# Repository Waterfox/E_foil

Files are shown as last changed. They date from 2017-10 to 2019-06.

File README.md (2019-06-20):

# Electric Hydrofoil Project

This is an electric hydrofoil thruster design.

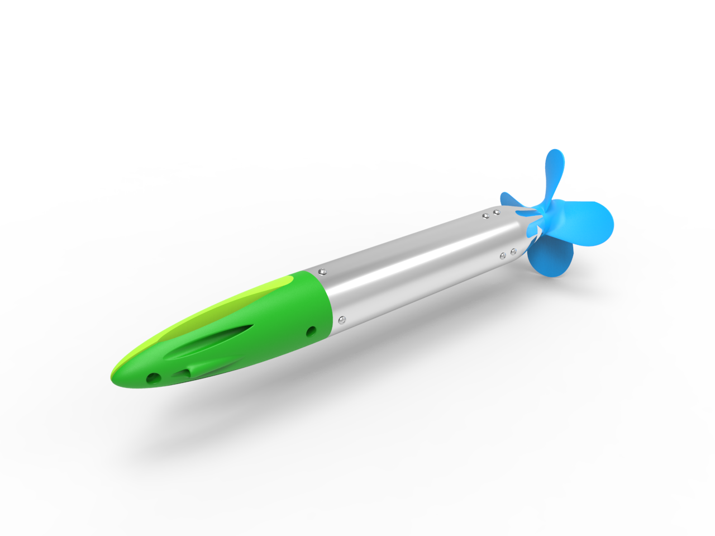
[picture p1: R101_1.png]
Thurster Render


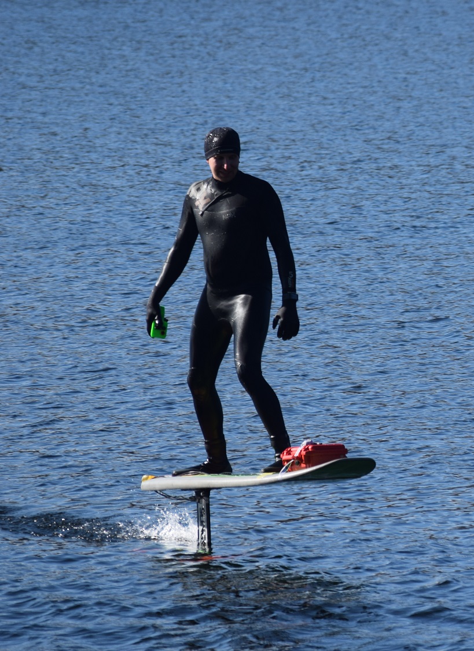
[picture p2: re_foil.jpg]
Riding Shot


Check out some of the initial test runs here on a Slingshot NF2 foil. 

[Waterproof Remote Control](https://github.com/Waterfox/Efoil-Waterproof-Controller)

<a href="http://www.youtube.com/watch?feature=player_embedded&v=rsEWBcoidBg
" target="_blank">IMAGE ALT TEXT HERE</a>

<a href="http://www.youtube.com/watch?feature=player_embedded&v=VSeLOgUywpE
" target="_blank">IMAGE ALT TEXT HERE</a>

<a href="http://www.youtube.com/watch?feature=player_embedded&v=JIKbu8u5FK8
" target="_blank">IMAGE ALT TEXT HERE</a>

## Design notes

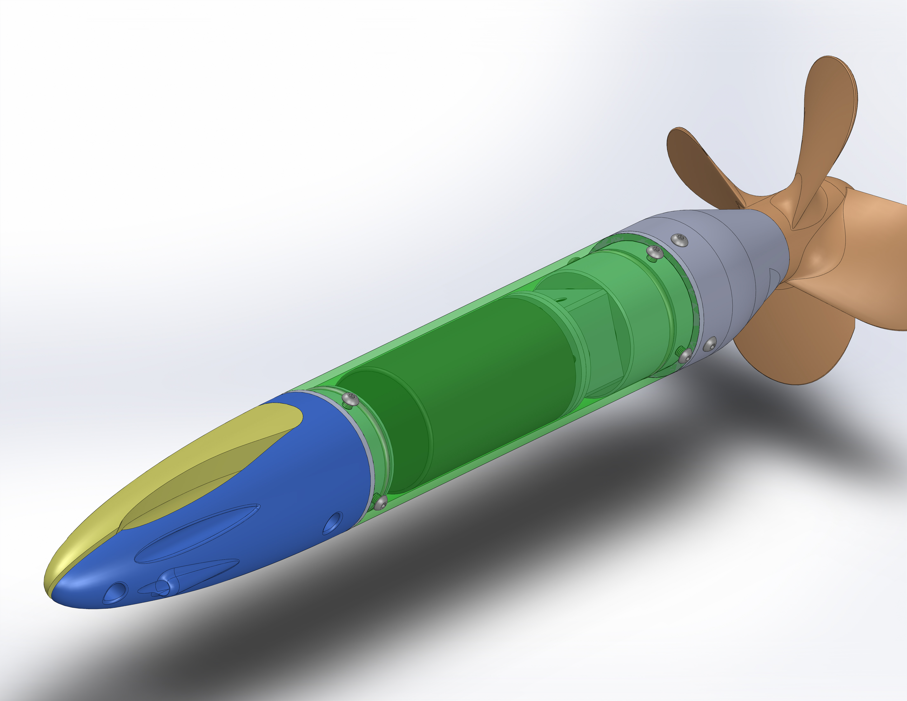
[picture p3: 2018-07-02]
R001_1 - Kitefoil Thruster Assy1.JPG

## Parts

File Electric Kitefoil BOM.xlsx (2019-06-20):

Part | Name | Description | Supplier | Part number | Cost | Currency | QTY | Mass kg | Website
R001 | Kitefoil Thruster Assy
R002 | SSS56104 500kV | Brushless Motor | Ebay |  | 160 | USD | 1 | 1.02 | http://www.ebay.com/itm/SSS-56104-500KV-6-pole-brushless-motor-/152600709580
R003 | gearbox | Neugart PLE40-008 | Ebay |  | 150 | USD | 1 | 0.35 | http://www.ebay.com/itm/NEUGART-PLE-40-GEARHEAD-REDUCER-FREE-SHIP-/251343315130
R004 | BHCS M4X0.7X6MM 18-8 |  | Mcmaster | 92095A188 |  |  | 16 |  | 92095A188
R005 | FHCS M4 X 0.7 X 8MM 18-8 |  | Mcmaster | 92125A188 | 6.5 |  | 10 |  | 92125A188
R006 | O-Ring 1/8 | 2.25 OD 2.0ID, 1/8in Dash 226 Buna-N | Mcmaster | 9452K64 | 13 | USD | 3 |  | https://www.mcmaster.com/#9452k64/=18ufglf
R007 | ESC | Hobbywing Seaking HV V3 130A | Ebay |  | 150 | USD | 1
R008 | Controller | 2.4Ghz Eskate Remote - with waterproof modification? | Ali-Express |  | 36 | USD | 1 |  | https://www.aliexpress.com/item/2-4Ghz-Remote-Controller-With-Receiver-Universal-for-All-ESC-Electric-Skateboard-Longboard-Skate-Board-Scooter/32817830821.html
R009 | Battery | Tattu Plus 6S 16000mAh |  |  |  |  | 2
R010 | Pelican Case 1200 | Pelican Case 1200 | MEC |  | 60 | CAD | 1
R011 | 8mm Shaft L= 65mm | 8mm ground shaft, 65MMLength | ? |  |  |  | 1
R012 | 8MM to 10MM Shaft Coupler | uxcell® 8mm to 10mm Elastic Shaft Coupling 30mm Length 25mm Diameter Motor Coupler Aluminum Alloy Joint Connector for DIY Encoder | Amazon | a16121900ux0451 | 10 | CAD | 1 |  | https://www.amazon.ca/dp/B06X9XSNQ2/ref=pe_3034960_233709270_TE_item
R013 | Oil Seal Bushing |  |  |  |  |  | 2
R014 | Bearing 8MM ID 11MM OD | 6153K51 | Mcmaster | 6153K51 | 12 | USD | 1 |  | 6153K51
R015 | Thrust Bearing |  | Mcmaster | 5909K11 | 3.7 | USD | 1
R015 | Thrust Bearing Washer |  | Mcmaster | 5909K71 |  |  | 2
 | Propeller shaft attachment | TBD |  |  |  |  | 1
 | 8, 10, or 12 AWG wire
 | Epoxy or Acrylic glue
 | M4 X 10MM ? | mount gearbox |  |  |  |  | 4
 | M3 X 10MM | oil seal cap |  |  |  |  | 1
 | M4 X 25MM | nose cone to front cap |  |  |  |  | 4
 | M5 X 25 | nose cone foil mount |  |  |  |  | 2
 | M5 NUT | nose cone foil mount |  |  |  |  | 2
MTS Parts
R101 | motor tube | 2.5IN OD 0.125IN WALL, 12IN Length 6061 T6 Tube | Online Metals, Mcmaster, Metal Supermarkets |  | 20 | CAD | 1 | 0.325
R102 | motor_gear_adapter_A | 6061-T6 0.125IN
R103 | motor_gear_adapter_B | 6061-T6 0.125IN
R104 | front_cap | 6061-T6 2.5IN ROUND BAR
R105 | gear_mount | 6061-T6 2.5IN ROUND BAR
R106 | shaft_cap | 6061-T6 2.5IN ROUND BAR
R107 | nose_cone_A | 3D PRINT PLA
P108 | nose_cone_B | 3D PRINT PLA
R109 | propeller | 3D PRINT PLA
R110 | reverse bushing | 3D PRINT PLA
R111 | Mast wire fairing | 3D PRINT PLA

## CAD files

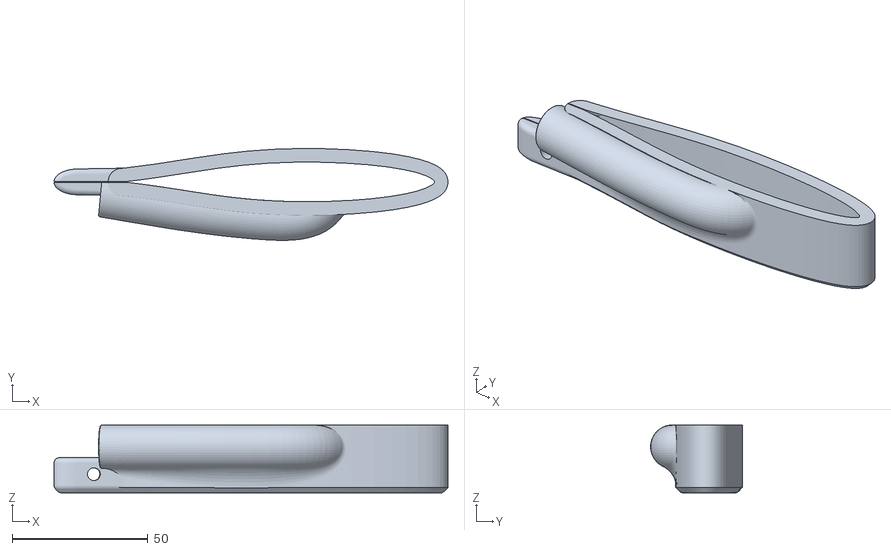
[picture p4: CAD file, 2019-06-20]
R111_1 - mast, wire fairing.STL
144.9 x 33.8 x 25.0

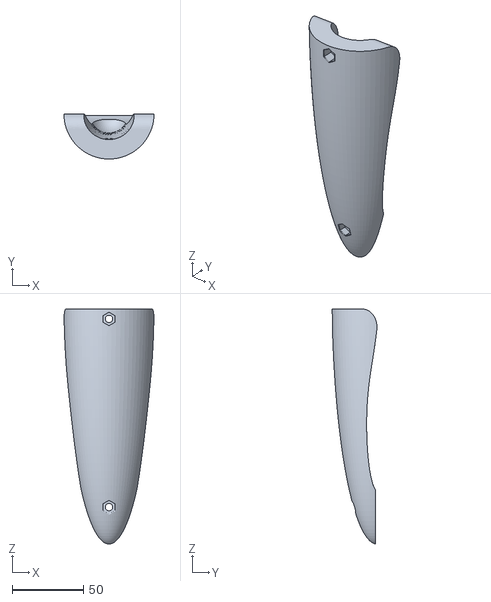
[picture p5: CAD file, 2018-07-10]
R108-GEO_2 - nose_cone_B.STL
63.0 x 31.6 x 164.9

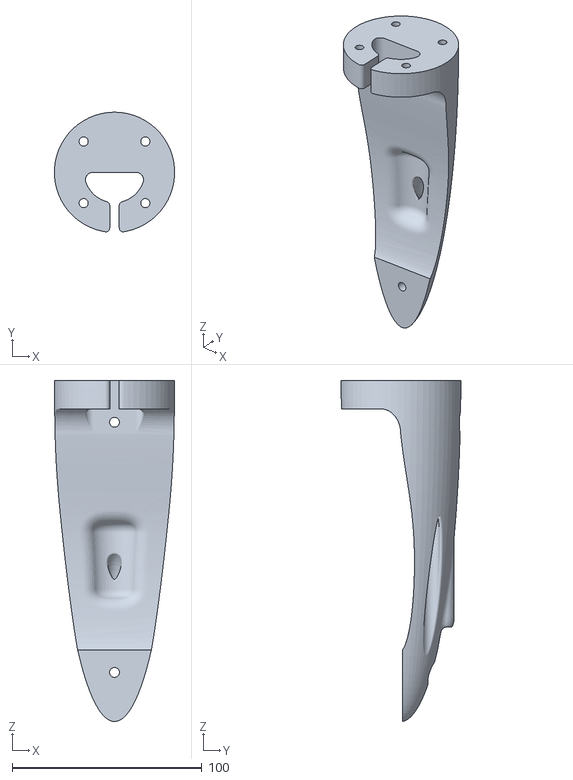
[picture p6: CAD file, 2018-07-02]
R107-GEO_2 - nose_cone_A.STL
63.4 x 63.2 x 179.9

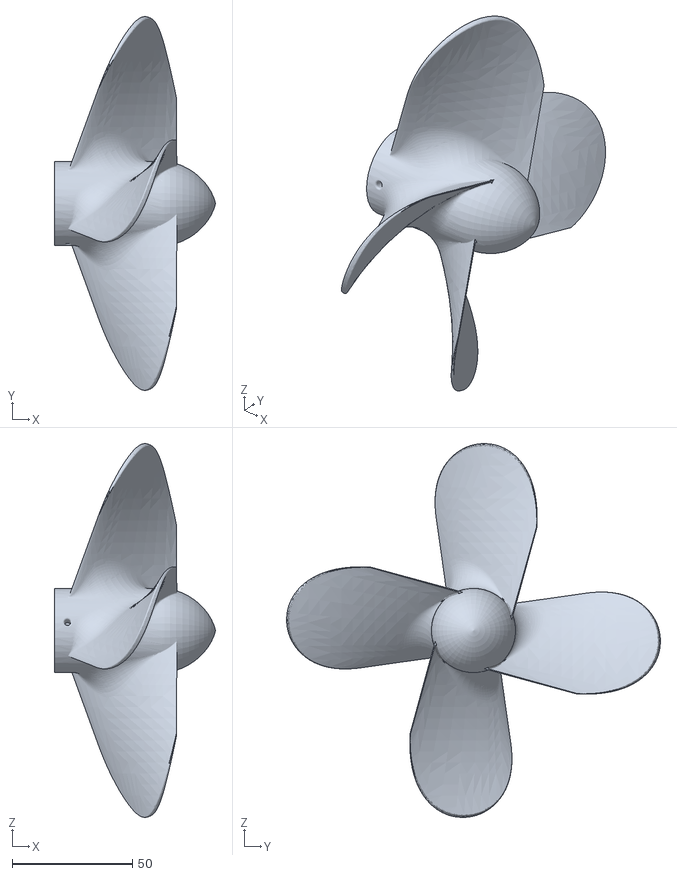
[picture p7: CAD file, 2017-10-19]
Propeller6_2_14kn4B.STL
67.0 x 155.4 x 155.4

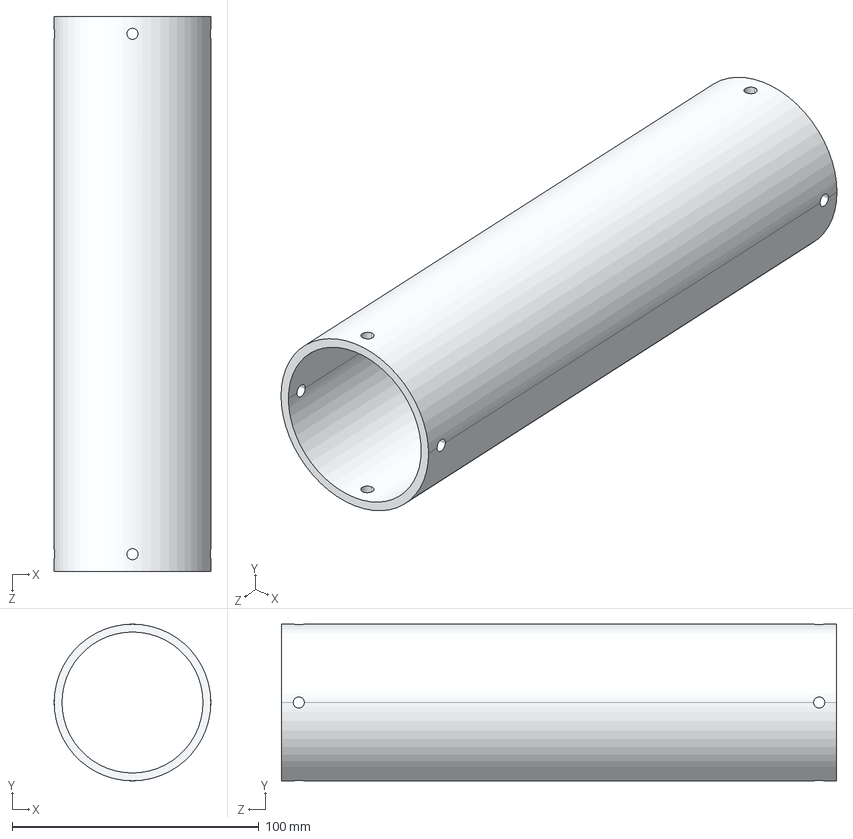
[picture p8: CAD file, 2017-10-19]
R101-GEO_1 - motor_tube.STEP
63.5 x 63.5 x 225.0 mm

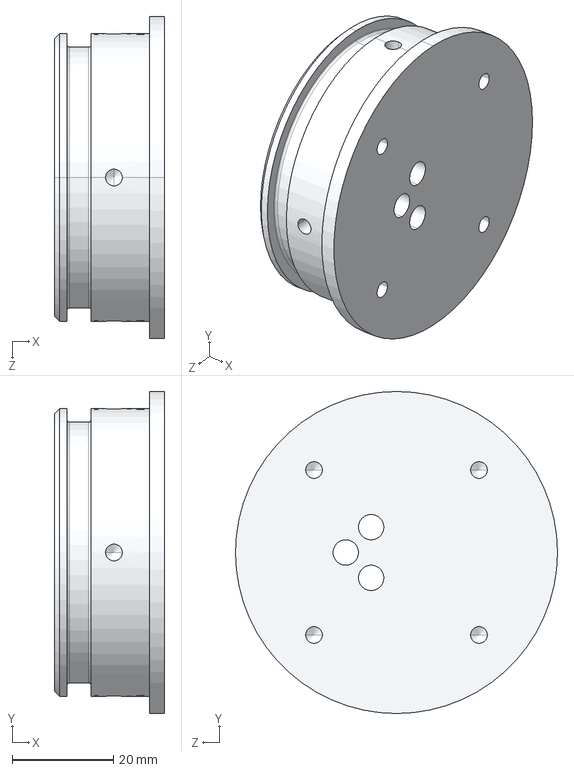
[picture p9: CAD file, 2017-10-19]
R104-GEO_1 - front_cap.STEP
21.7 x 63.5 x 63.5 mm

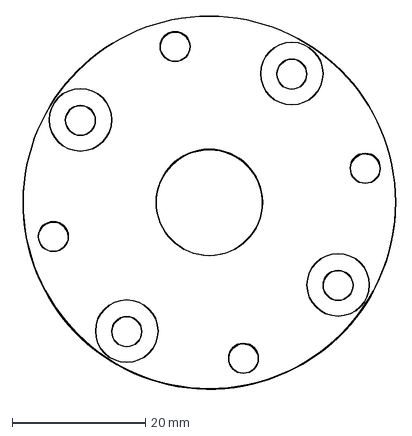
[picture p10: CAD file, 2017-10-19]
R102-GEO_1 - motor_gear_adapter_A.DXF
57.0 x 57.1 mm

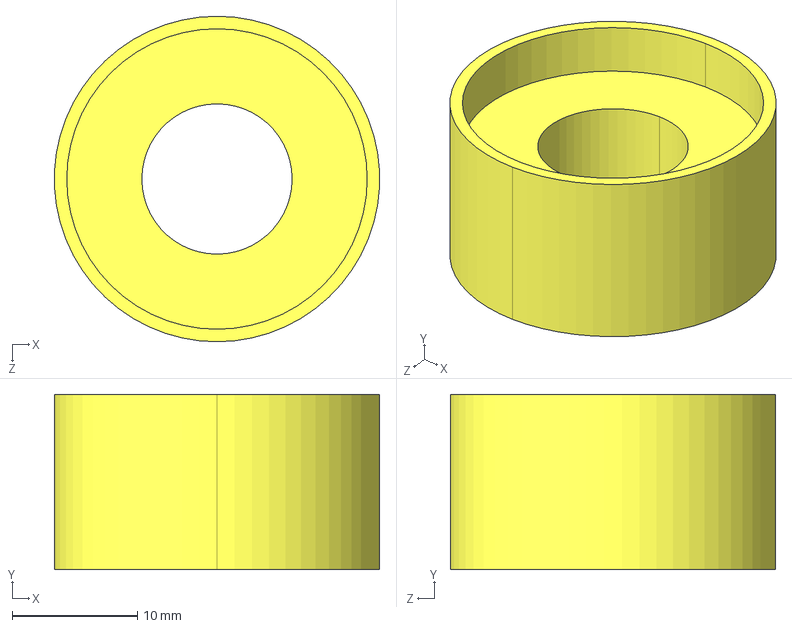
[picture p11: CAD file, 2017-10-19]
R109-GEO_1 - thrust_beaing-mount.STEP
26.0 x 14.0 x 26.0 mm

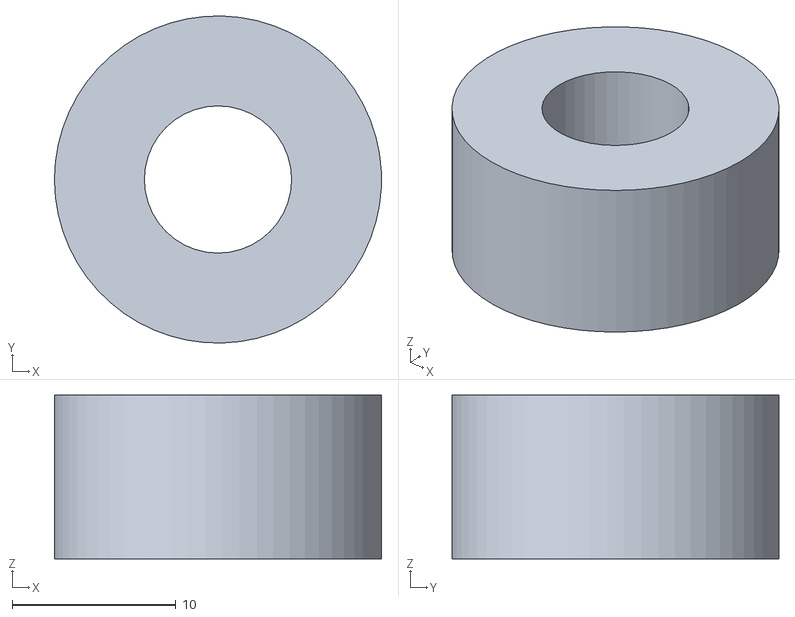
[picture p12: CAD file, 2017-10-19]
R110-GEO_2 - revBushing.STL
20.0 x 20.0 x 10.0

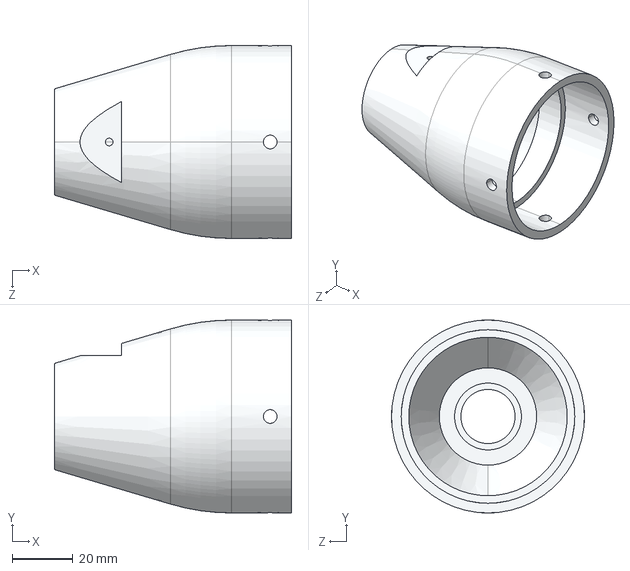
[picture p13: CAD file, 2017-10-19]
R106-GEO_1 - shaft_cap.STEP
78.0 x 63.5 x 63.5 mm

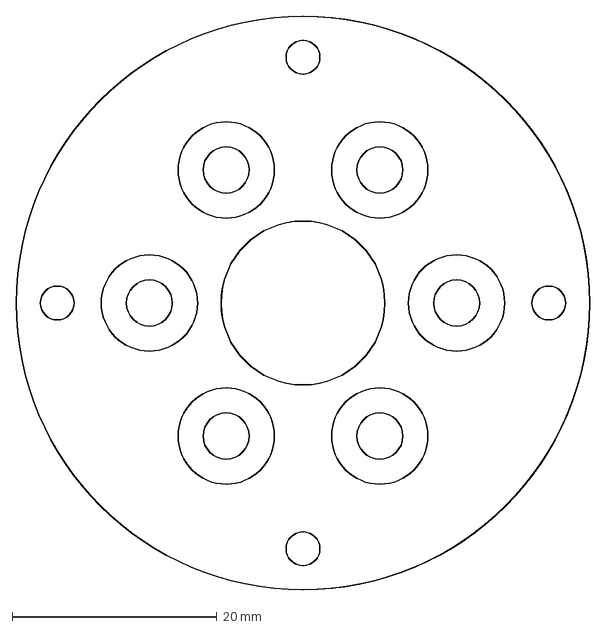
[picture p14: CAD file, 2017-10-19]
R103-GEO_1 - motor_gear_adapter_B.DXF
56.0 x 56.0 mm

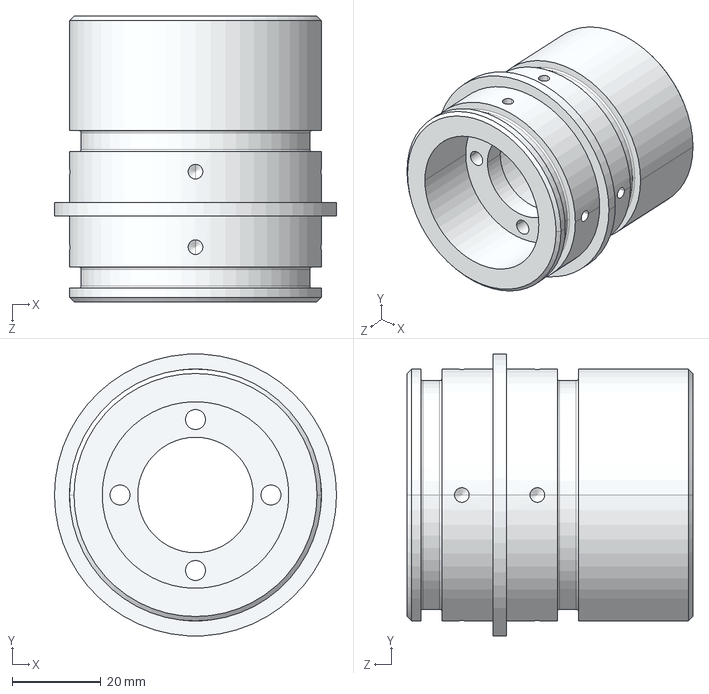
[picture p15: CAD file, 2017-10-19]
R105-GEO_1 - gear_mount.STEP
63.5 x 63.4 x 64.3 mm

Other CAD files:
Mast - wire fairing.STL

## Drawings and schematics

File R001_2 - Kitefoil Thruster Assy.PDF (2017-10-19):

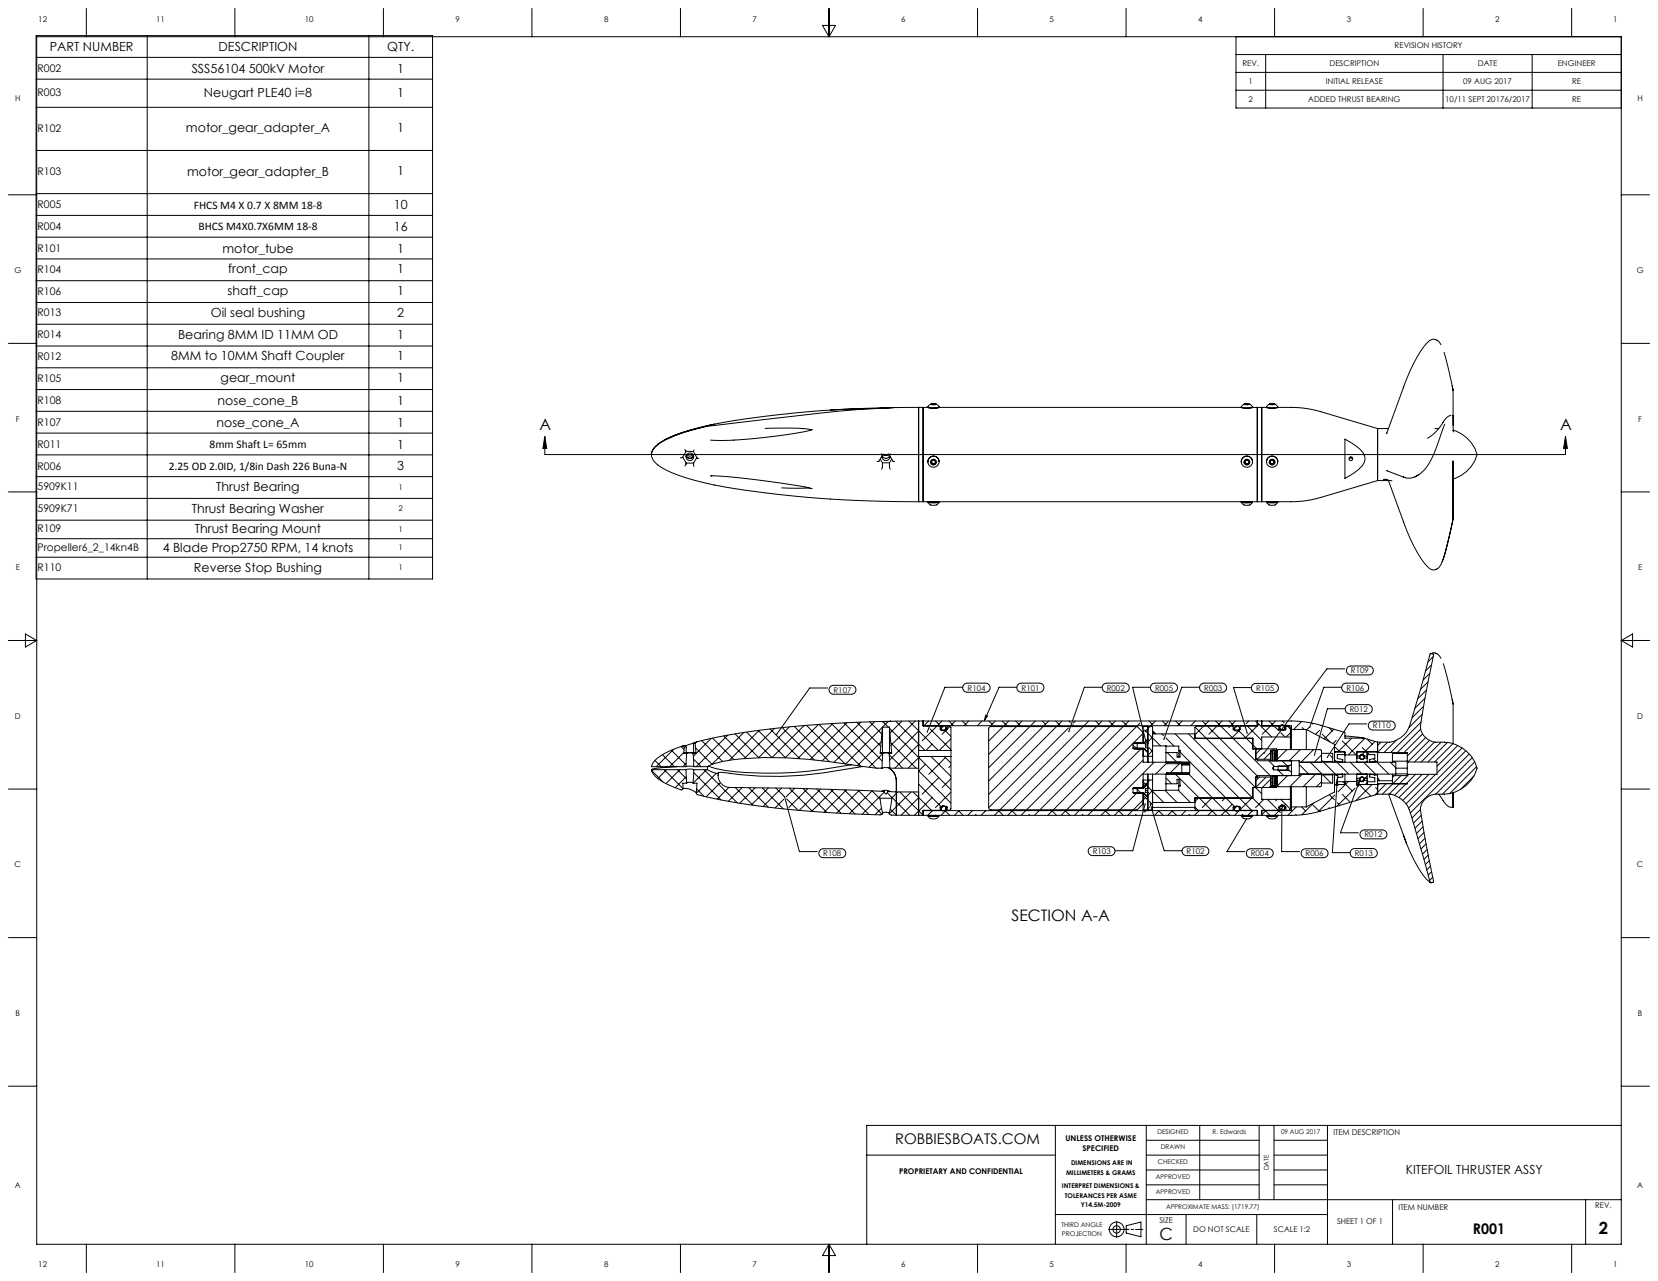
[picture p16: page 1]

R002 | SSS56104 500kV Motor | 1
R003 | Neugart PLE40 i=8 | 1

REV. | DESCRIPTION | DATE | ENGINEER
1 | INITIAL RELEASE | 09 AUG 2017 | RE
2 | ADDED THRUST BEARING | 10/11 SEPT 20176/2017 | RE

R102 | motor_gear_adapter_A | 1

R103 | motor_gear_adapter_B | 1

R005 | FHCS M4 X 0.7 X 8MM 18-8 | 10
R004 | BHCS M4X0.7X6MM 18-8 | 16
R101 | motor_tube | 1
R104 | front_cap | 1
R106 | shaft_cap | 1
R013 | Oil seal bushing | 2
R014 | Bearing 8MM ID 11MM OD | 1
R012 | 8MM to 10MM Shaft Coupler | 1
R105 | gear_mount | 1
R108 | nose_cone_B | 1
R107 | nose_cone_A | 1
R011 | 8mm Shaft L= 65mm | 1
R006 | 2.25 OD 2.0ID, 1/8in Dash 226 Buna-N | 3
5909K11 | Thrust Bearing | 1
5909K71 | Thrust Bearing Washer | 2
R109 | Thrust Bearing Mount | 1
Propeller6_2_14kn4B | 4 Blade Prop2750 RPM, 14 knots | 1
R110 | Reverse Stop Bushing | 1

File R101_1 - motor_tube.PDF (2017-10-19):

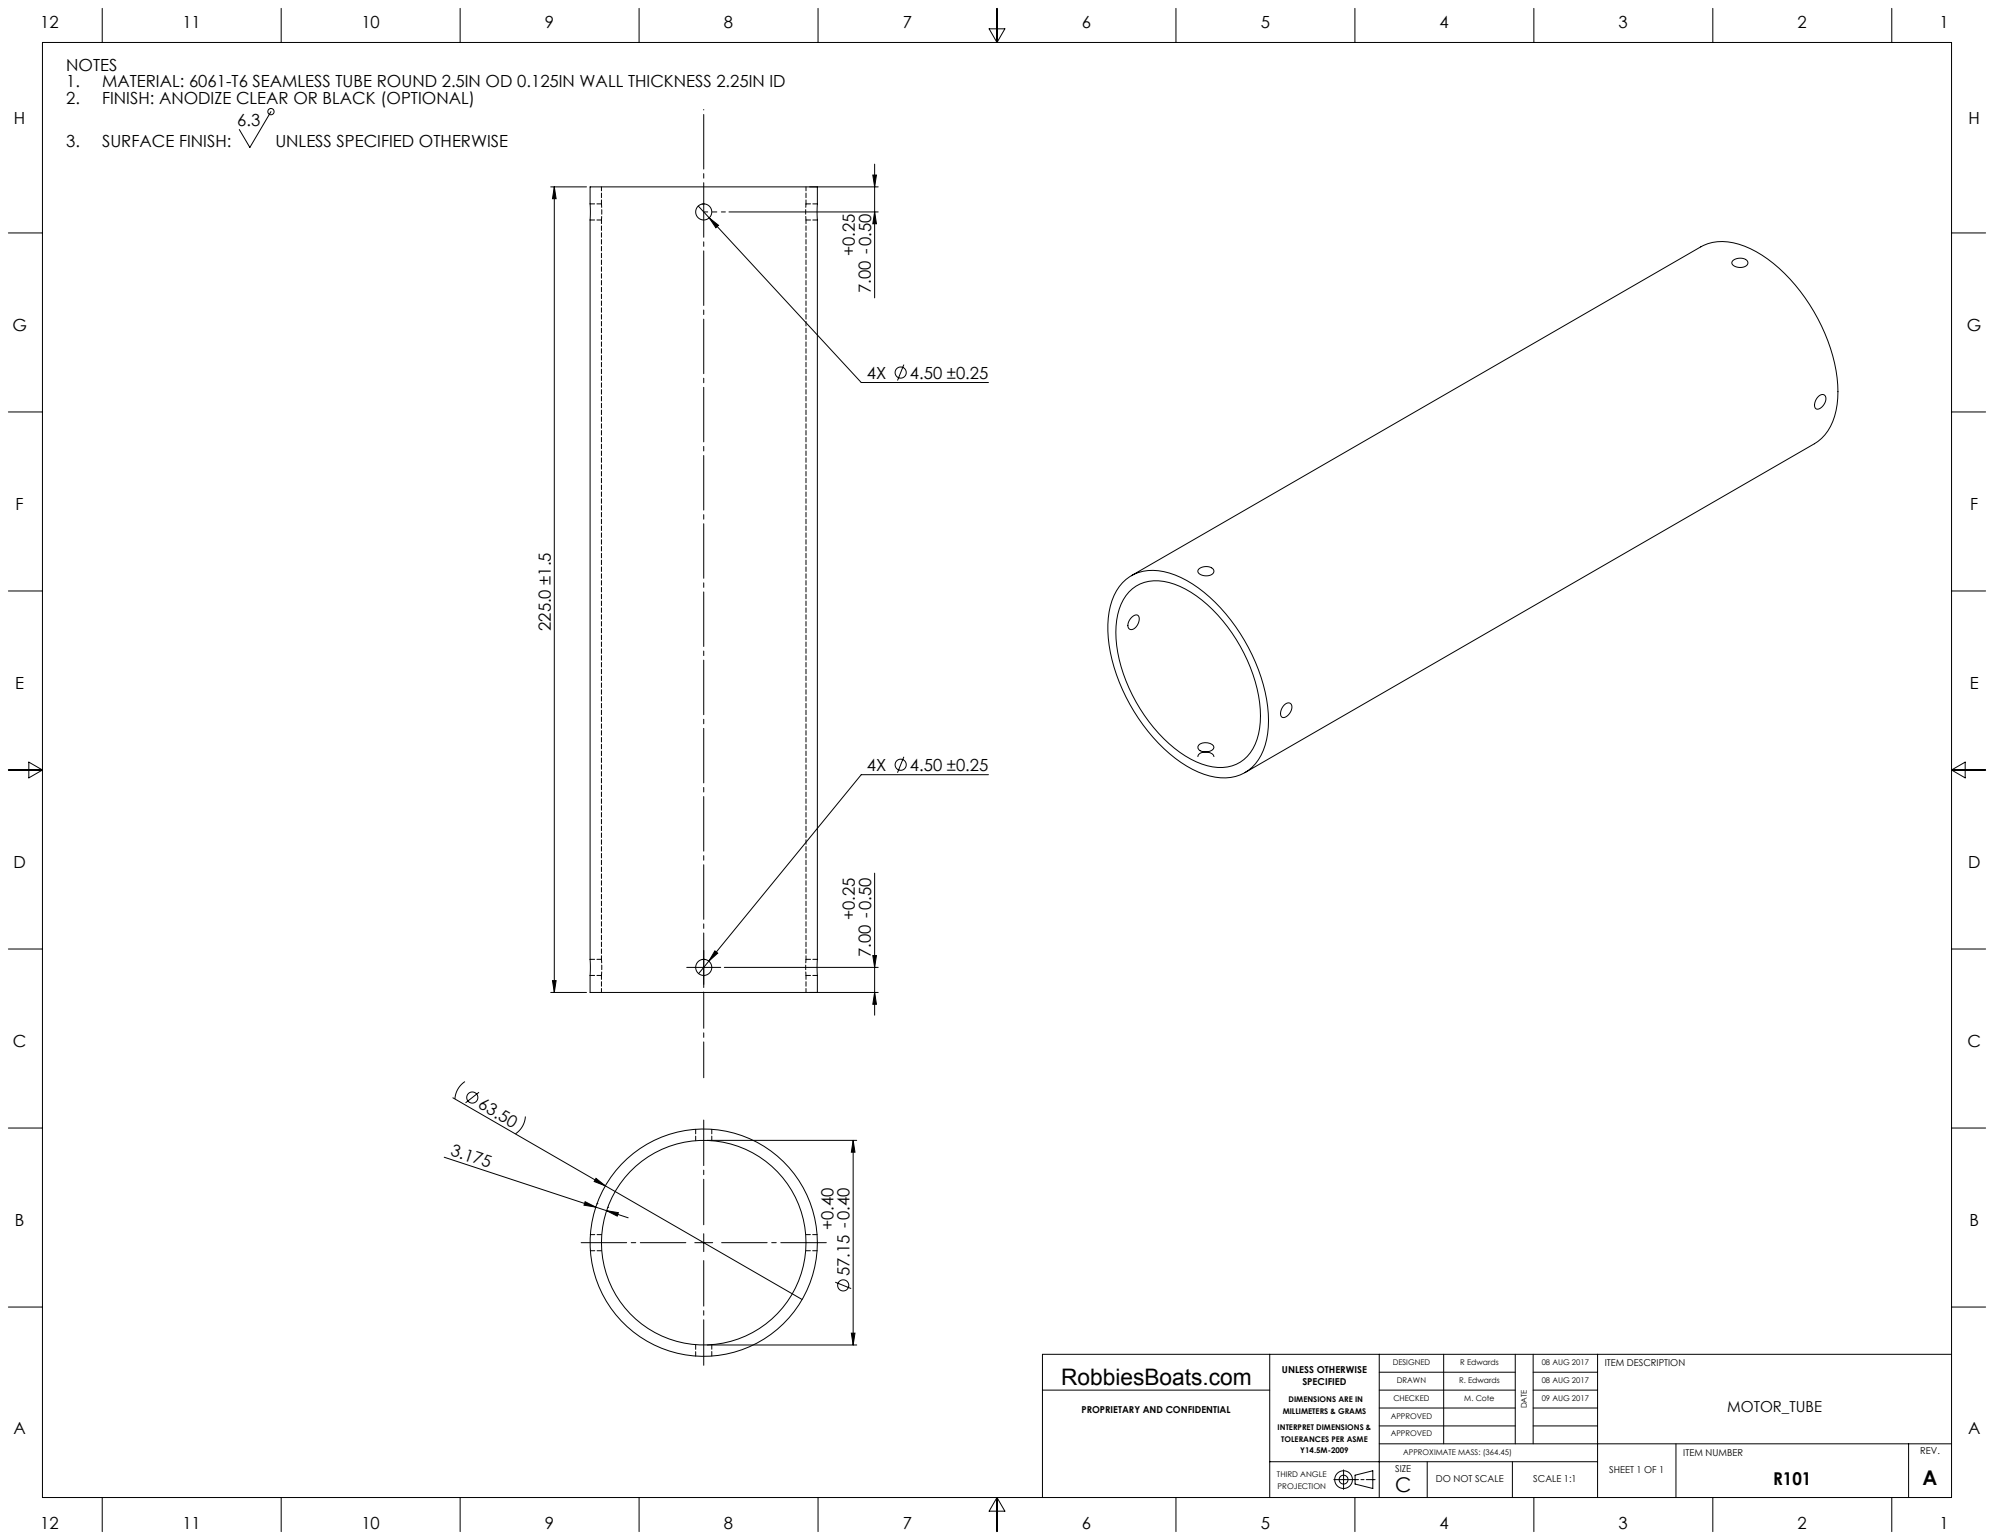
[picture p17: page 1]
THIRD ANGLE; C DO NOT SCALE; R Edwards; R. Edwards; M. Cote; 08 AUG 2017; 09 AUG 2017; APPROXIMATE MASS: (364.45); ITEM NUMBER; SHEET 1 OF 1; SCALE 1:1; ITEM DESCRIPTION

NOTES
1. MATERIAL: 6061-T6 SEAMLESS TUBE ROUND 2.5IN OD 0.125IN WALL THICKNESS 2.25IN ID
2. FINISH: ANODIZE CLEAR OR BLACK (OPTIONAL)
3. UNLESS SPECIFIED OTHERWISE
SURFACE FINISH:

UNLESS OTHERWISE
SPECIFIED
DIMENSIONS ARE IN
MILLIMETERS & GRAMS
INTERPRET DIMENSIONS &
TOLERANCES PER ASME

PROPRIETARY AND CONFIDENTIAL

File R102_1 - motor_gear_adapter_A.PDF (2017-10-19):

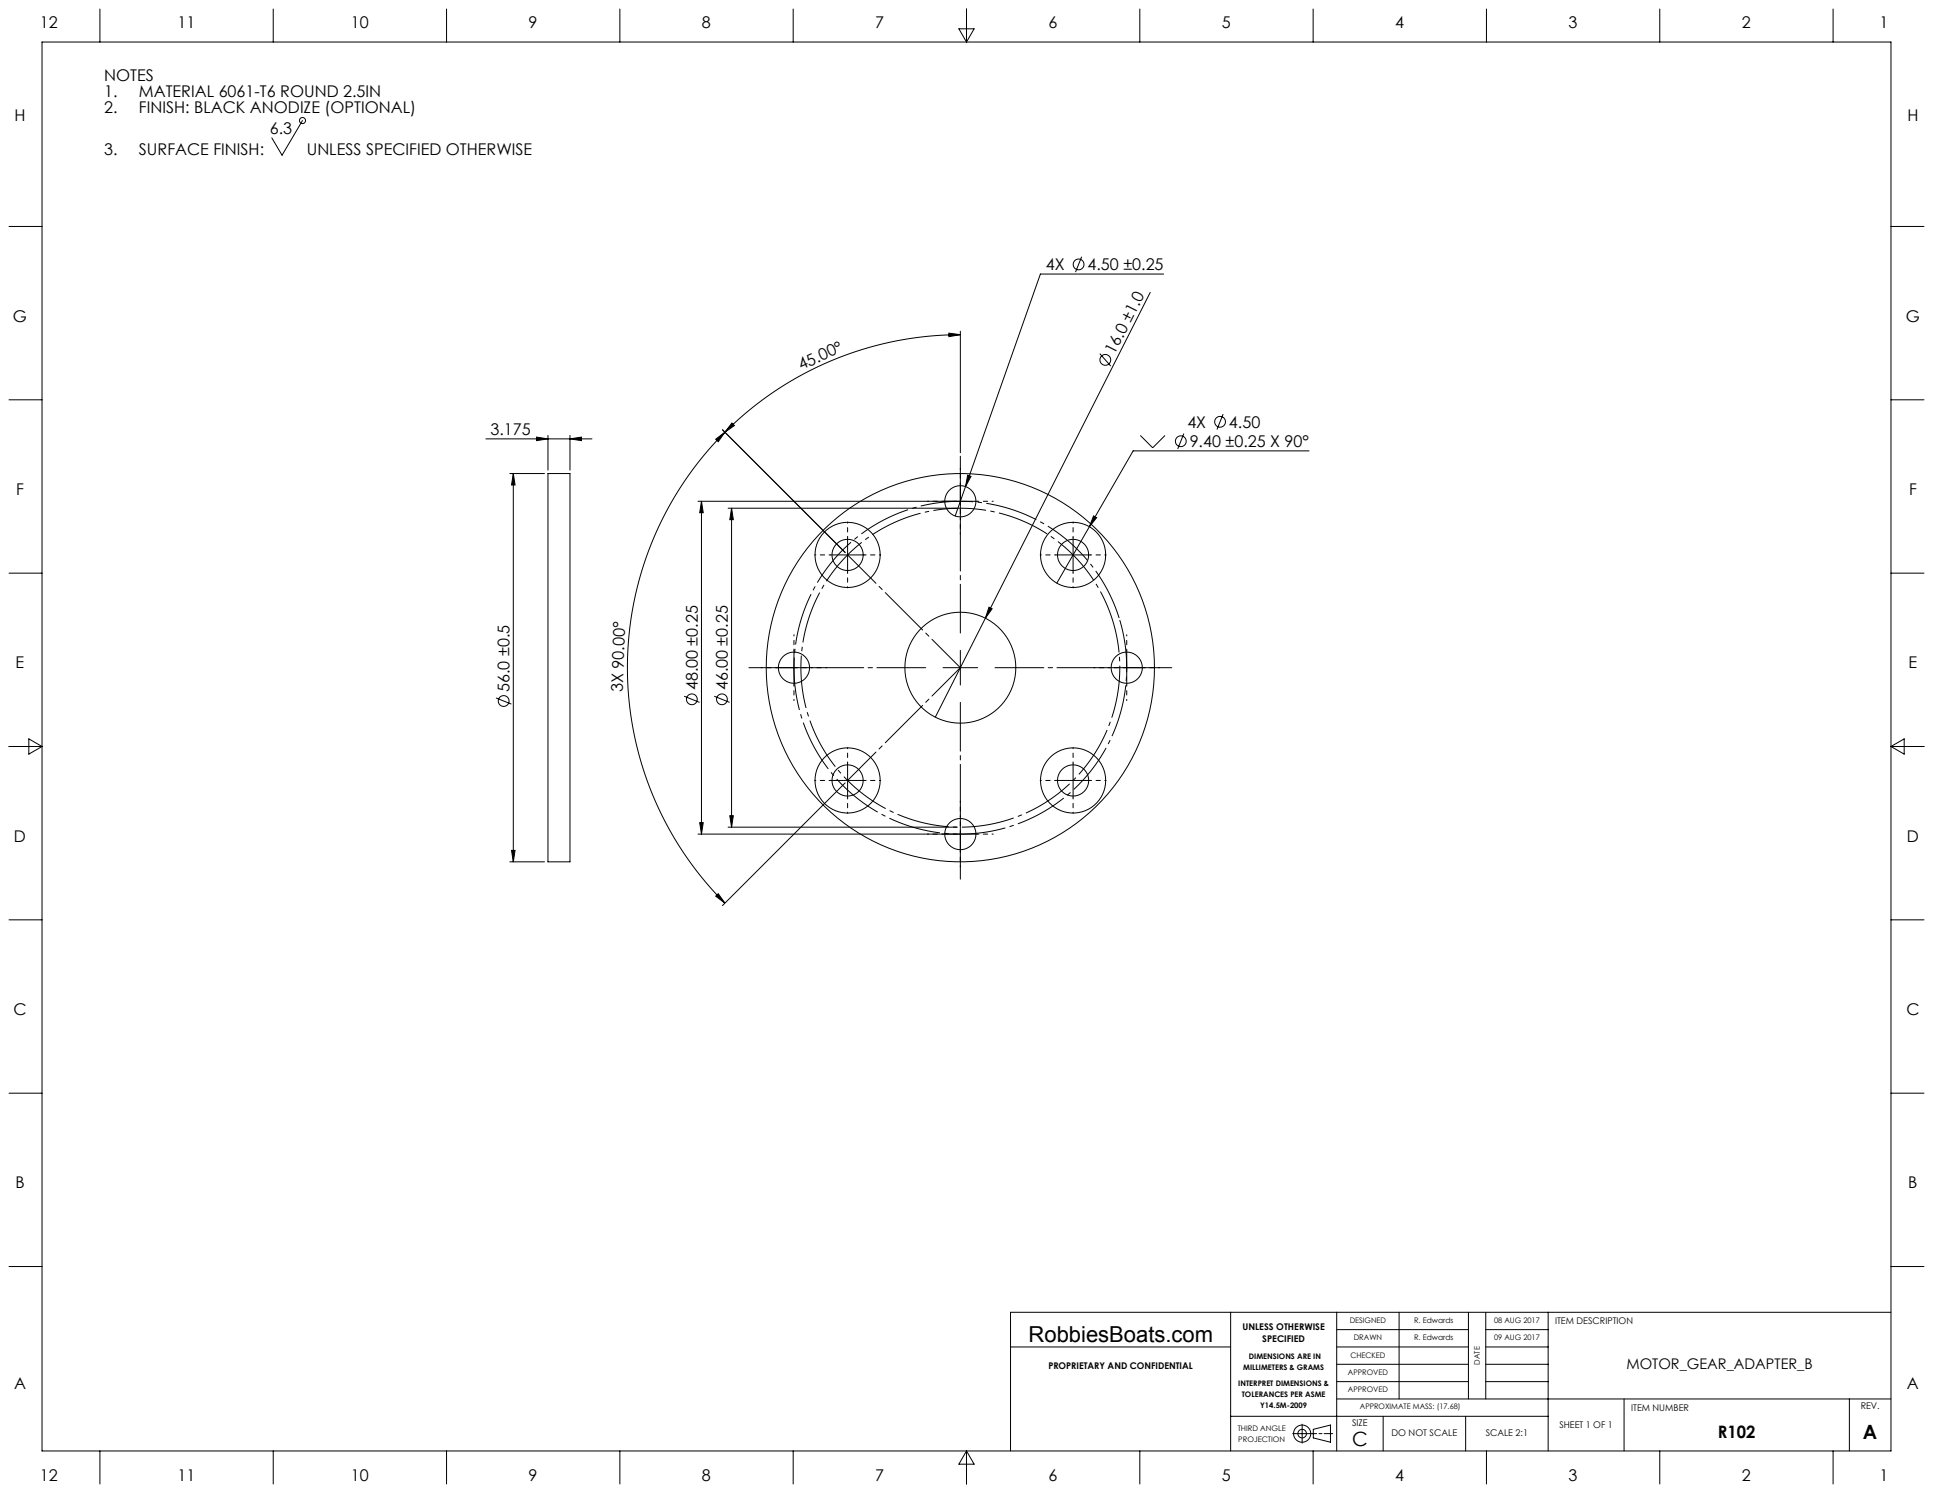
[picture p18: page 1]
SURFACE FINISH:; THIRD ANGLE; C DO NOT SCALE; R. Edwards; 08 AUG 2017; 09 AUG 2017; APPROXIMATE MASS: (17.68); ITEM NUMBER; SHEET 1 OF 1; SCALE 2:1; ITEM DESCRIPTION

NOTES
1. MATERIAL 6061-T6 ROUND 2.5IN
2. FINISH: BLACK ANODIZE (OPTIONAL)

3. UNLESS SPECIFIED OTHERWISE

UNLESS OTHERWISE
SPECIFIED
DIMENSIONS ARE IN
MILLIMETERS & GRAMS
INTERPRET DIMENSIONS &
TOLERANCES PER ASME

PROPRIETARY AND CONFIDENTIAL

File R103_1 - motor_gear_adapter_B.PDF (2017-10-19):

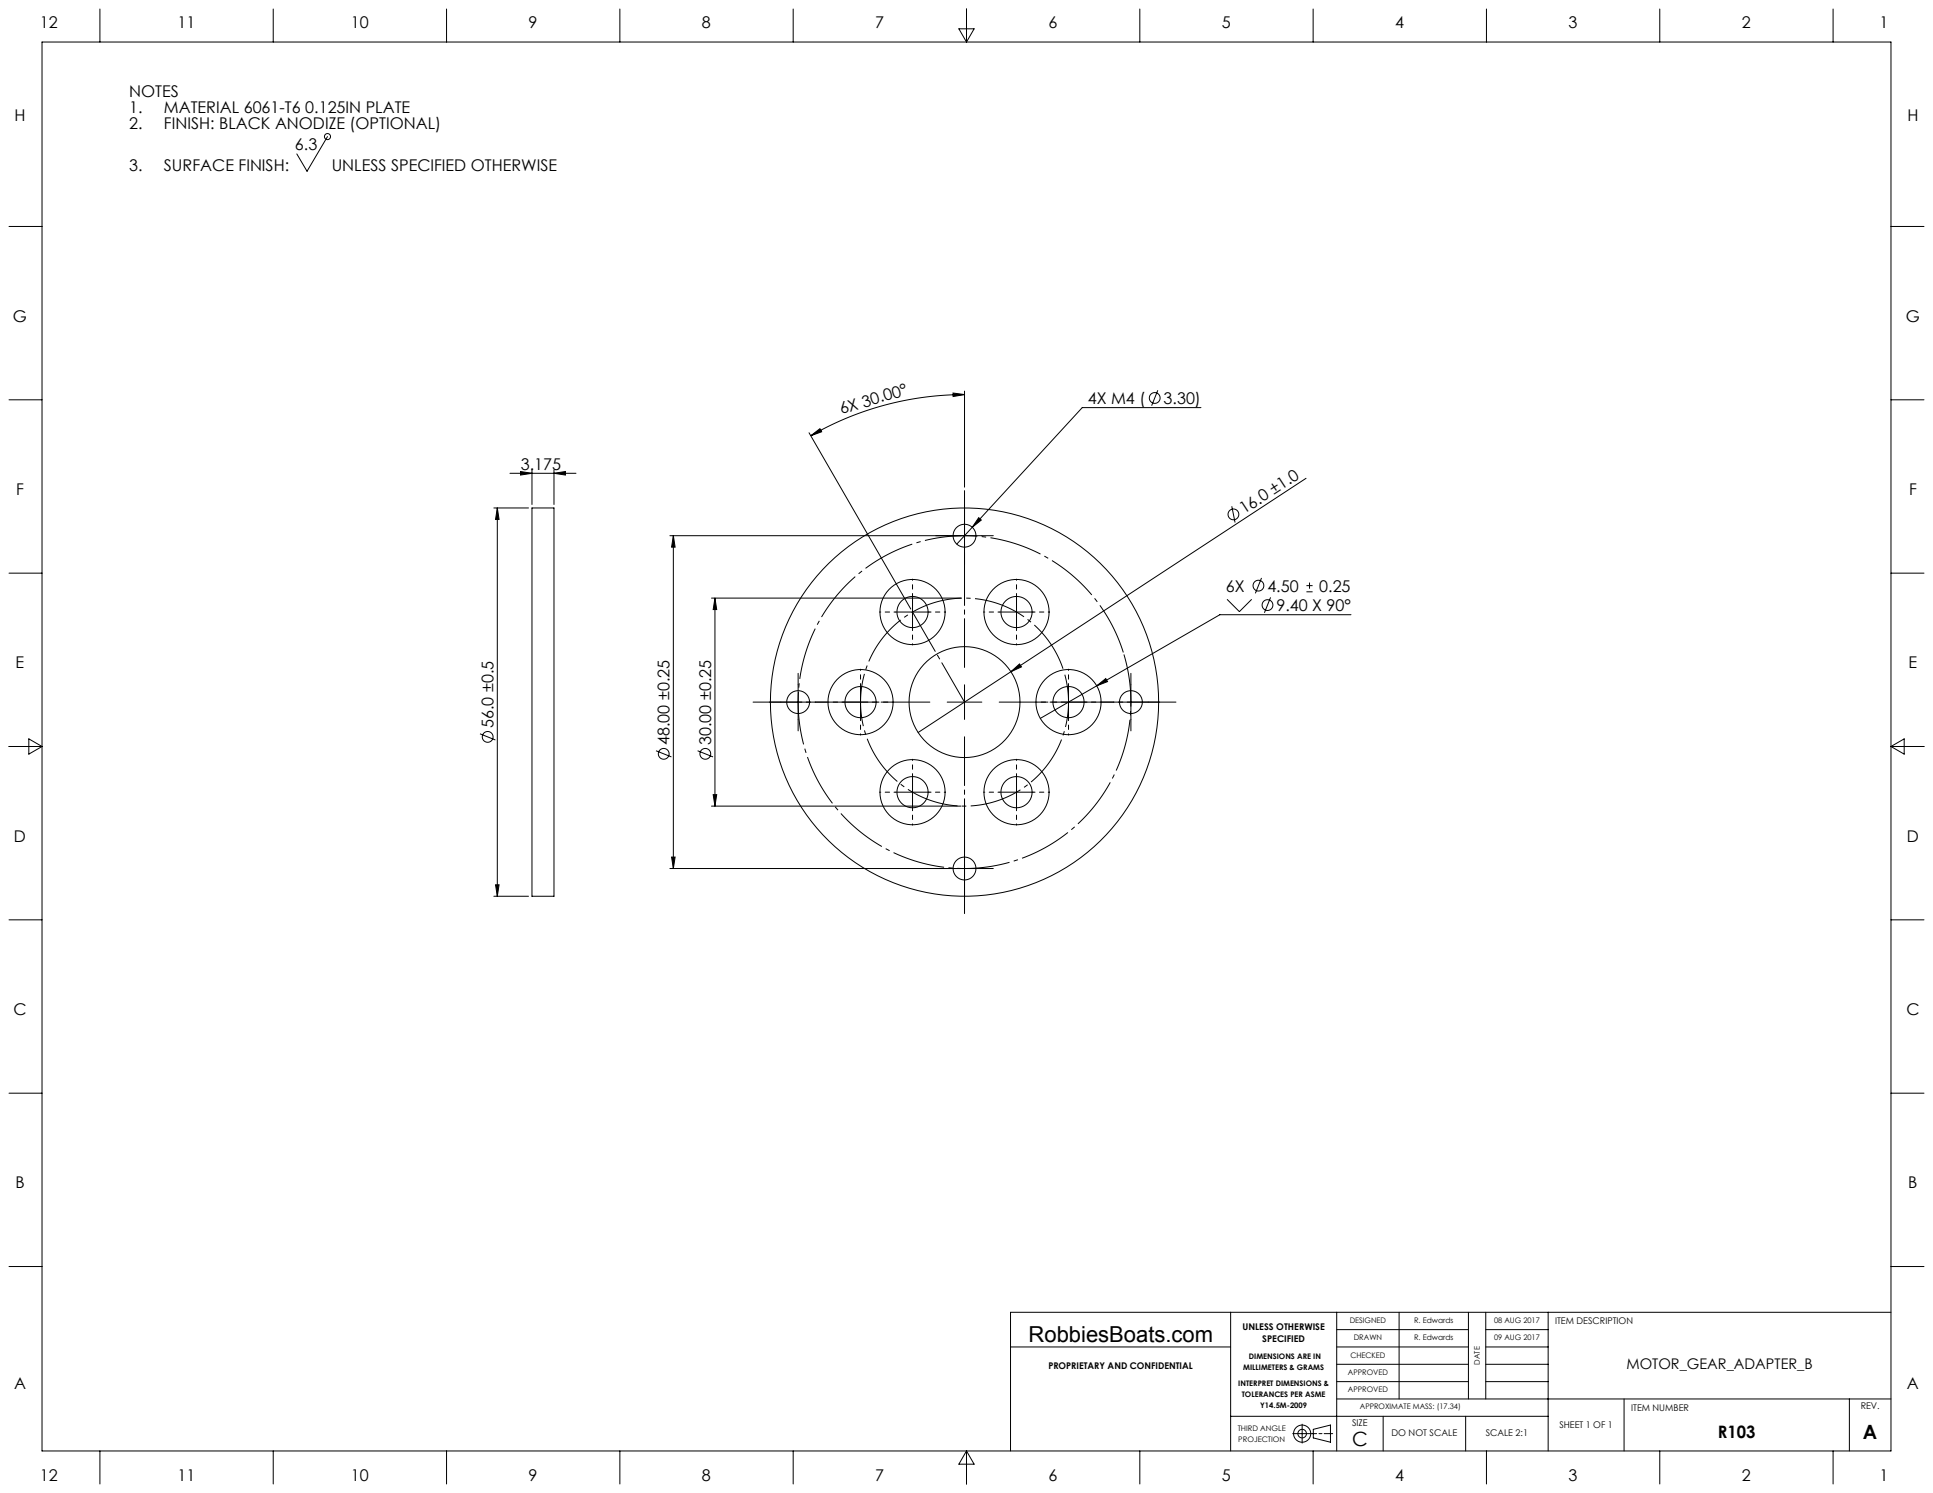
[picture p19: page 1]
SURFACE FINISH:; THIRD ANGLE; C DO NOT SCALE; R. Edwards; 08 AUG 2017; 09 AUG 2017; APPROXIMATE MASS: (17.34); ITEM NUMBER; SHEET 1 OF 1; SCALE 2:1; ITEM DESCRIPTION

NOTES
1. MATERIAL 6061-T6 0.125IN PLATE
2. FINISH: BLACK ANODIZE (OPTIONAL)

3. UNLESS SPECIFIED OTHERWISE

UNLESS OTHERWISE
SPECIFIED
DIMENSIONS ARE IN
MILLIMETERS & GRAMS
INTERPRET DIMENSIONS &
TOLERANCES PER ASME

PROPRIETARY AND CONFIDENTIAL

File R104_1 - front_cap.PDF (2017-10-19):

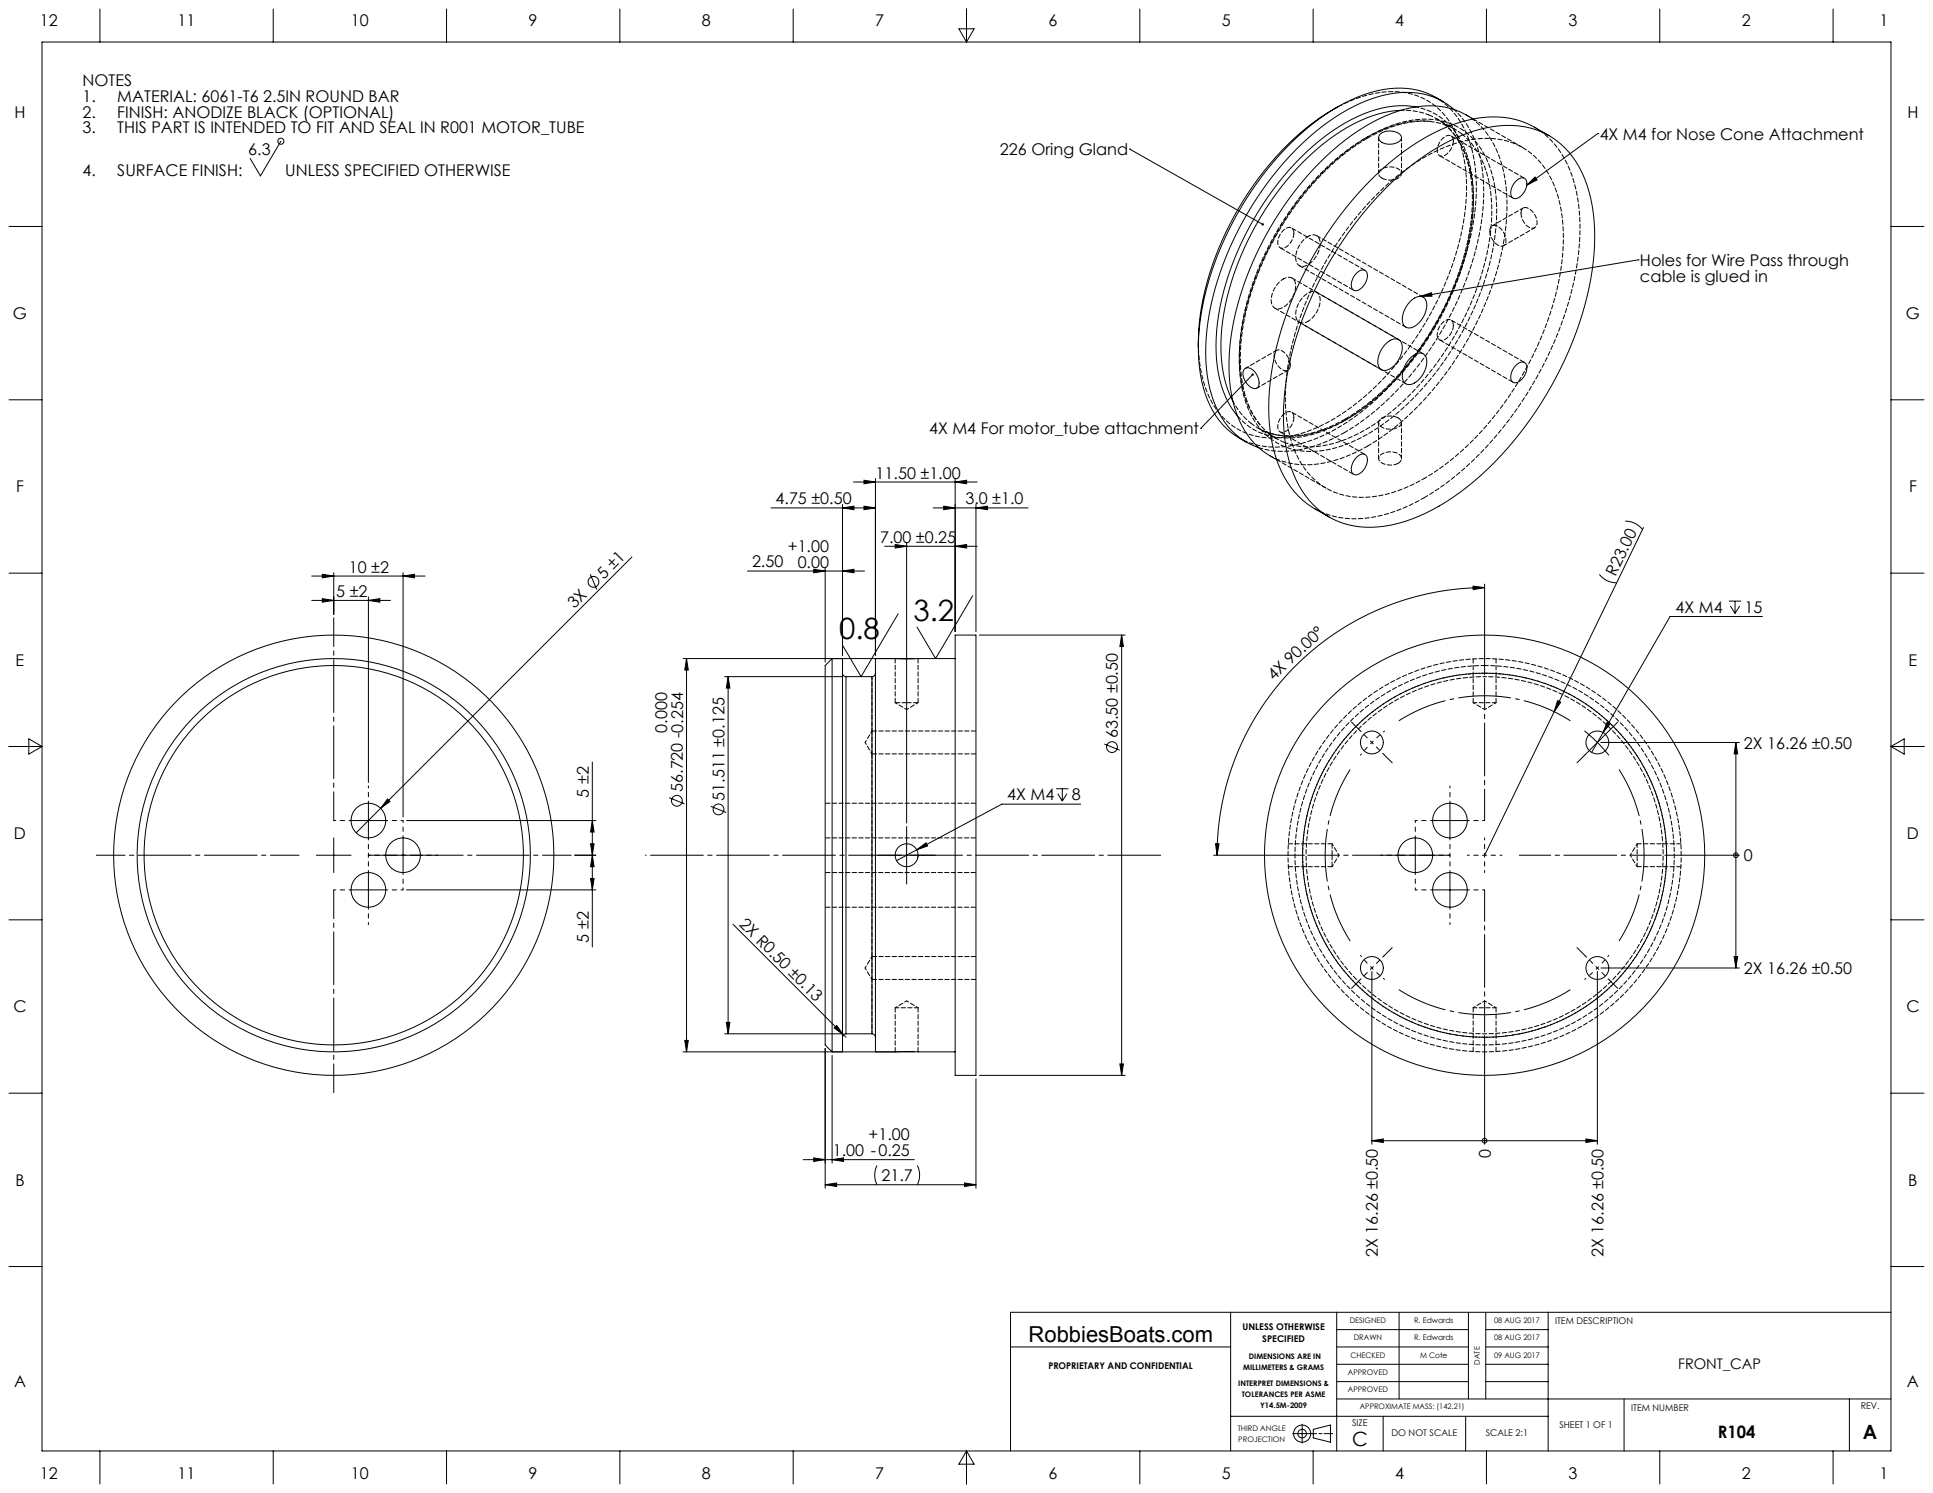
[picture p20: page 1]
226 Oring Gland; 4X M4 For motor_tube attachment; THIRD ANGLE; C DO NOT SCALE; R. Edwards; M Cote; 08 AUG 2017; 09 AUG 2017; APPROXIMATE MASS: (142.21); ITEM NUMBER; SHEET 1 OF 1; SCALE 2:1; ITEM DESCRIPTION

NOTES
1. MATERIAL: 6061-T6 2.5IN ROUND BAR
2. FINISH: ANODIZE BLACK (OPTIONAL)
3. THIS PART IS INTENDED TO FIT AND SEAL IN R001 MOTOR_TUBE

4X M4 for Nose Cone Attachment

SURFACE FINISH:
4. UNLESS SPECIFIED OTHERWISE

Holes for Wire Pass through
cable is glued in

UNLESS OTHERWISE
SPECIFIED
DIMENSIONS ARE IN
MILLIMETERS & GRAMS
INTERPRET DIMENSIONS &
TOLERANCES PER ASME

PROPRIETARY AND CONFIDENTIAL

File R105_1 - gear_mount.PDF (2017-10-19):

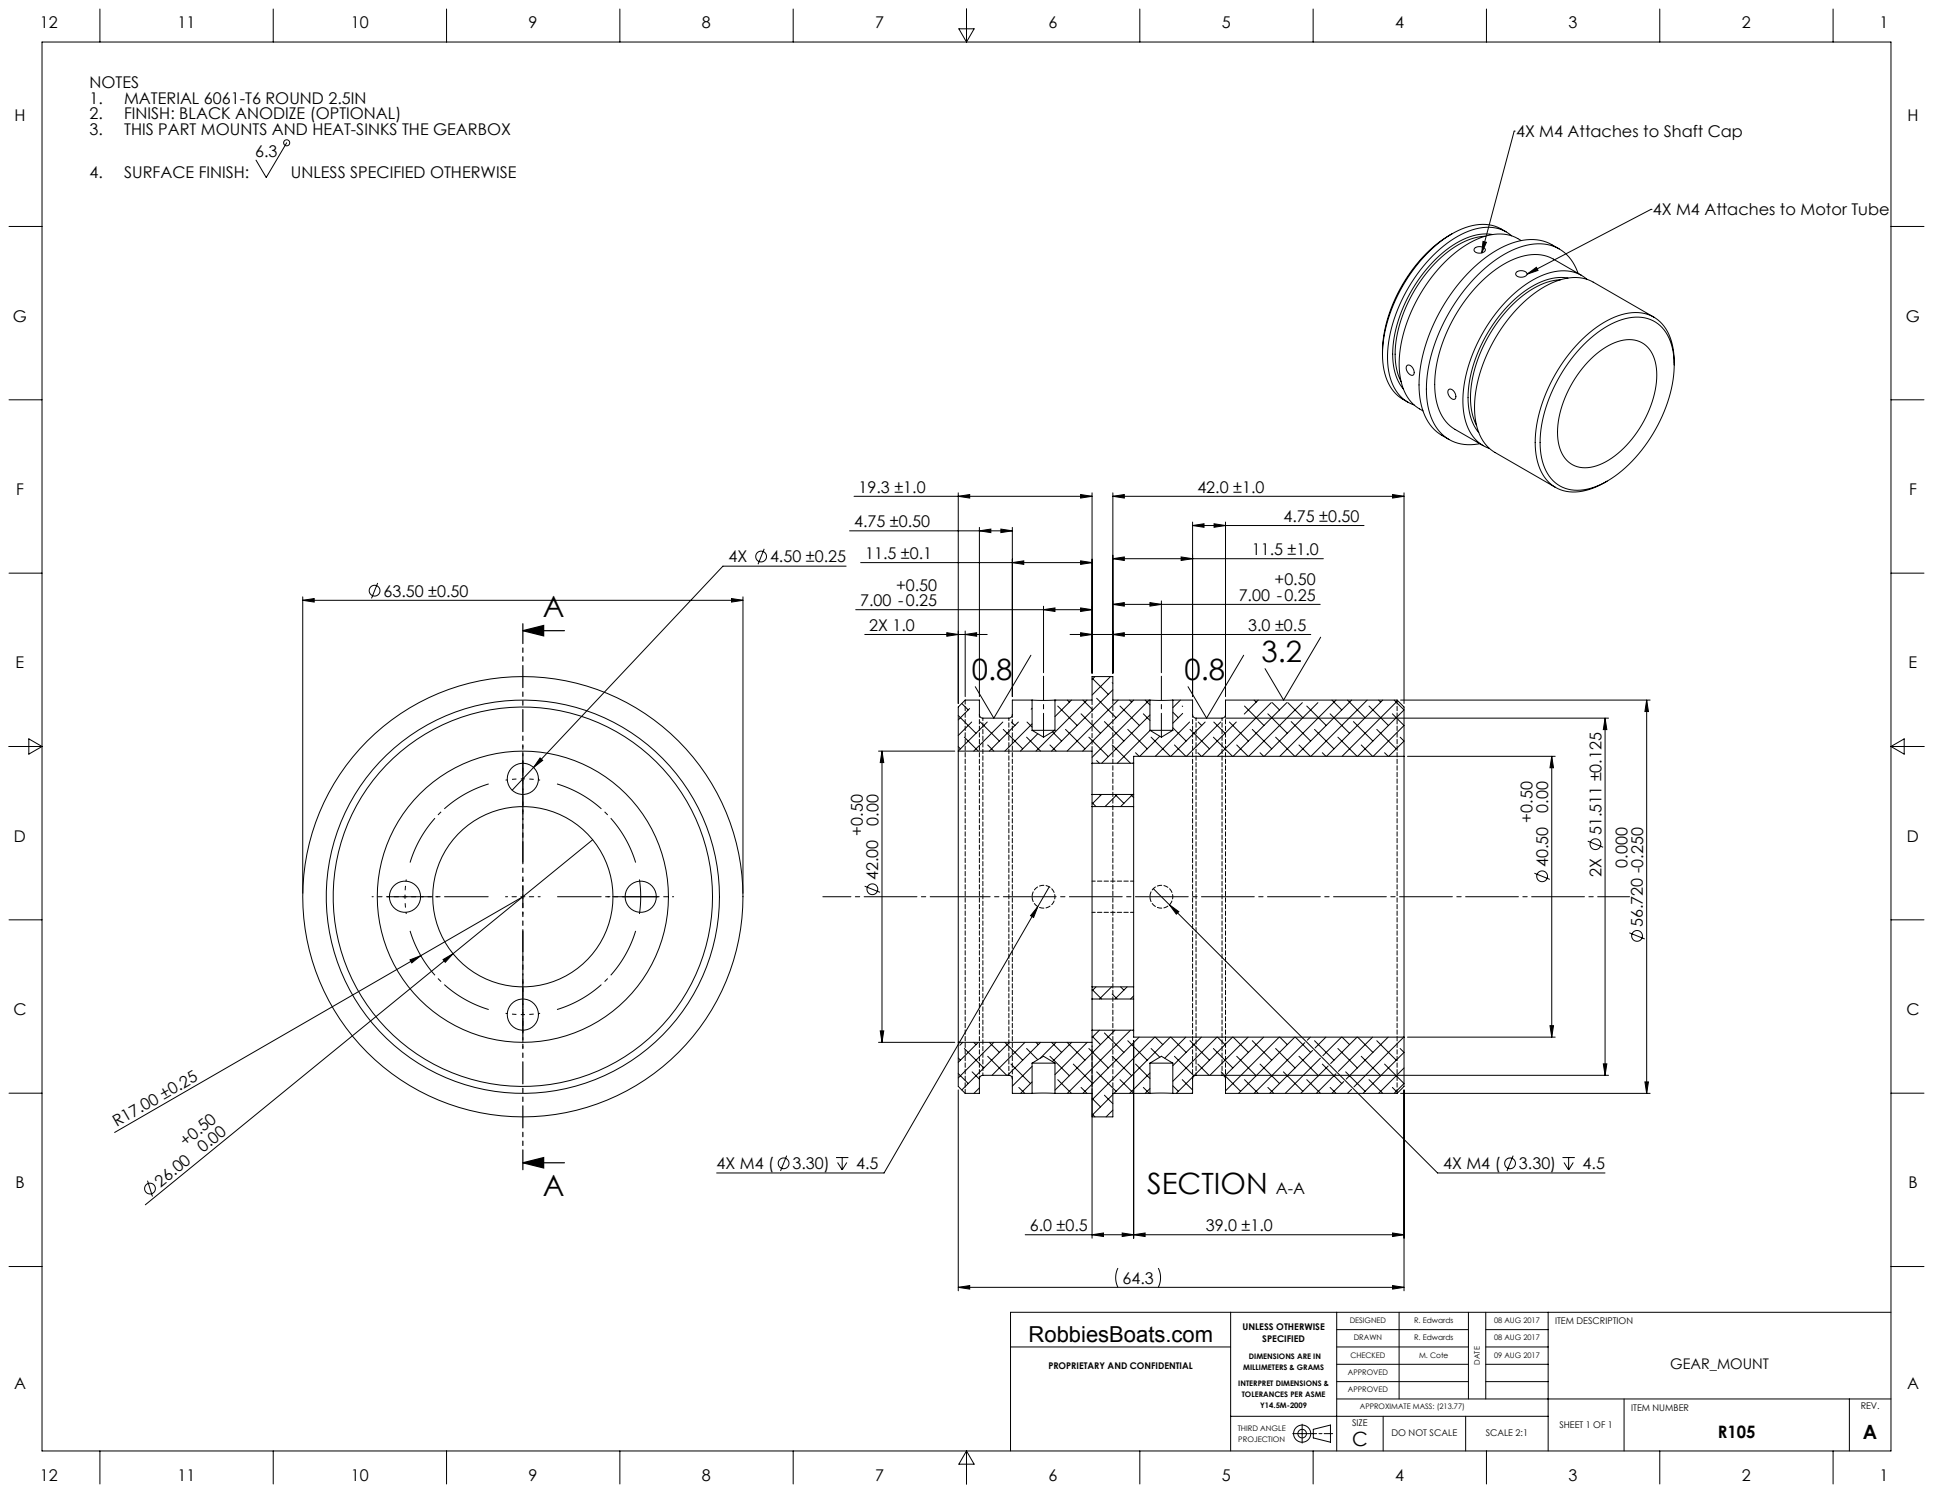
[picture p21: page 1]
SECTION A-A; SURFACE FINISH:; THIRD ANGLE; C DO NOT SCALE; R. Edwards; M. Cote; 08 AUG 2017; 09 AUG 2017; APPROXIMATE MASS: (213.77); ITEM NUMBER; SHEET 1 OF 1; SCALE 2:1; ITEM DESCRIPTION

4X M4 Attaches to Shaft Cap 56.720 -0.000 0.250 2X 51.511 ±0.125

NOTES
1. MATERIAL 6061-T6 ROUND 2.5IN
2. FINISH: BLACK ANODIZE (OPTIONAL)
3. THIS PART MOUNTS AND HEAT-SINKS THE GEARBOX

4. UNLESS SPECIFIED OTHERWISE

4X M4 Attaches to Motor Tube

UNLESS OTHERWISE
SPECIFIED
DIMENSIONS ARE IN
MILLIMETERS & GRAMS
INTERPRET DIMENSIONS &
TOLERANCES PER ASME

PROPRIETARY AND CONFIDENTIAL

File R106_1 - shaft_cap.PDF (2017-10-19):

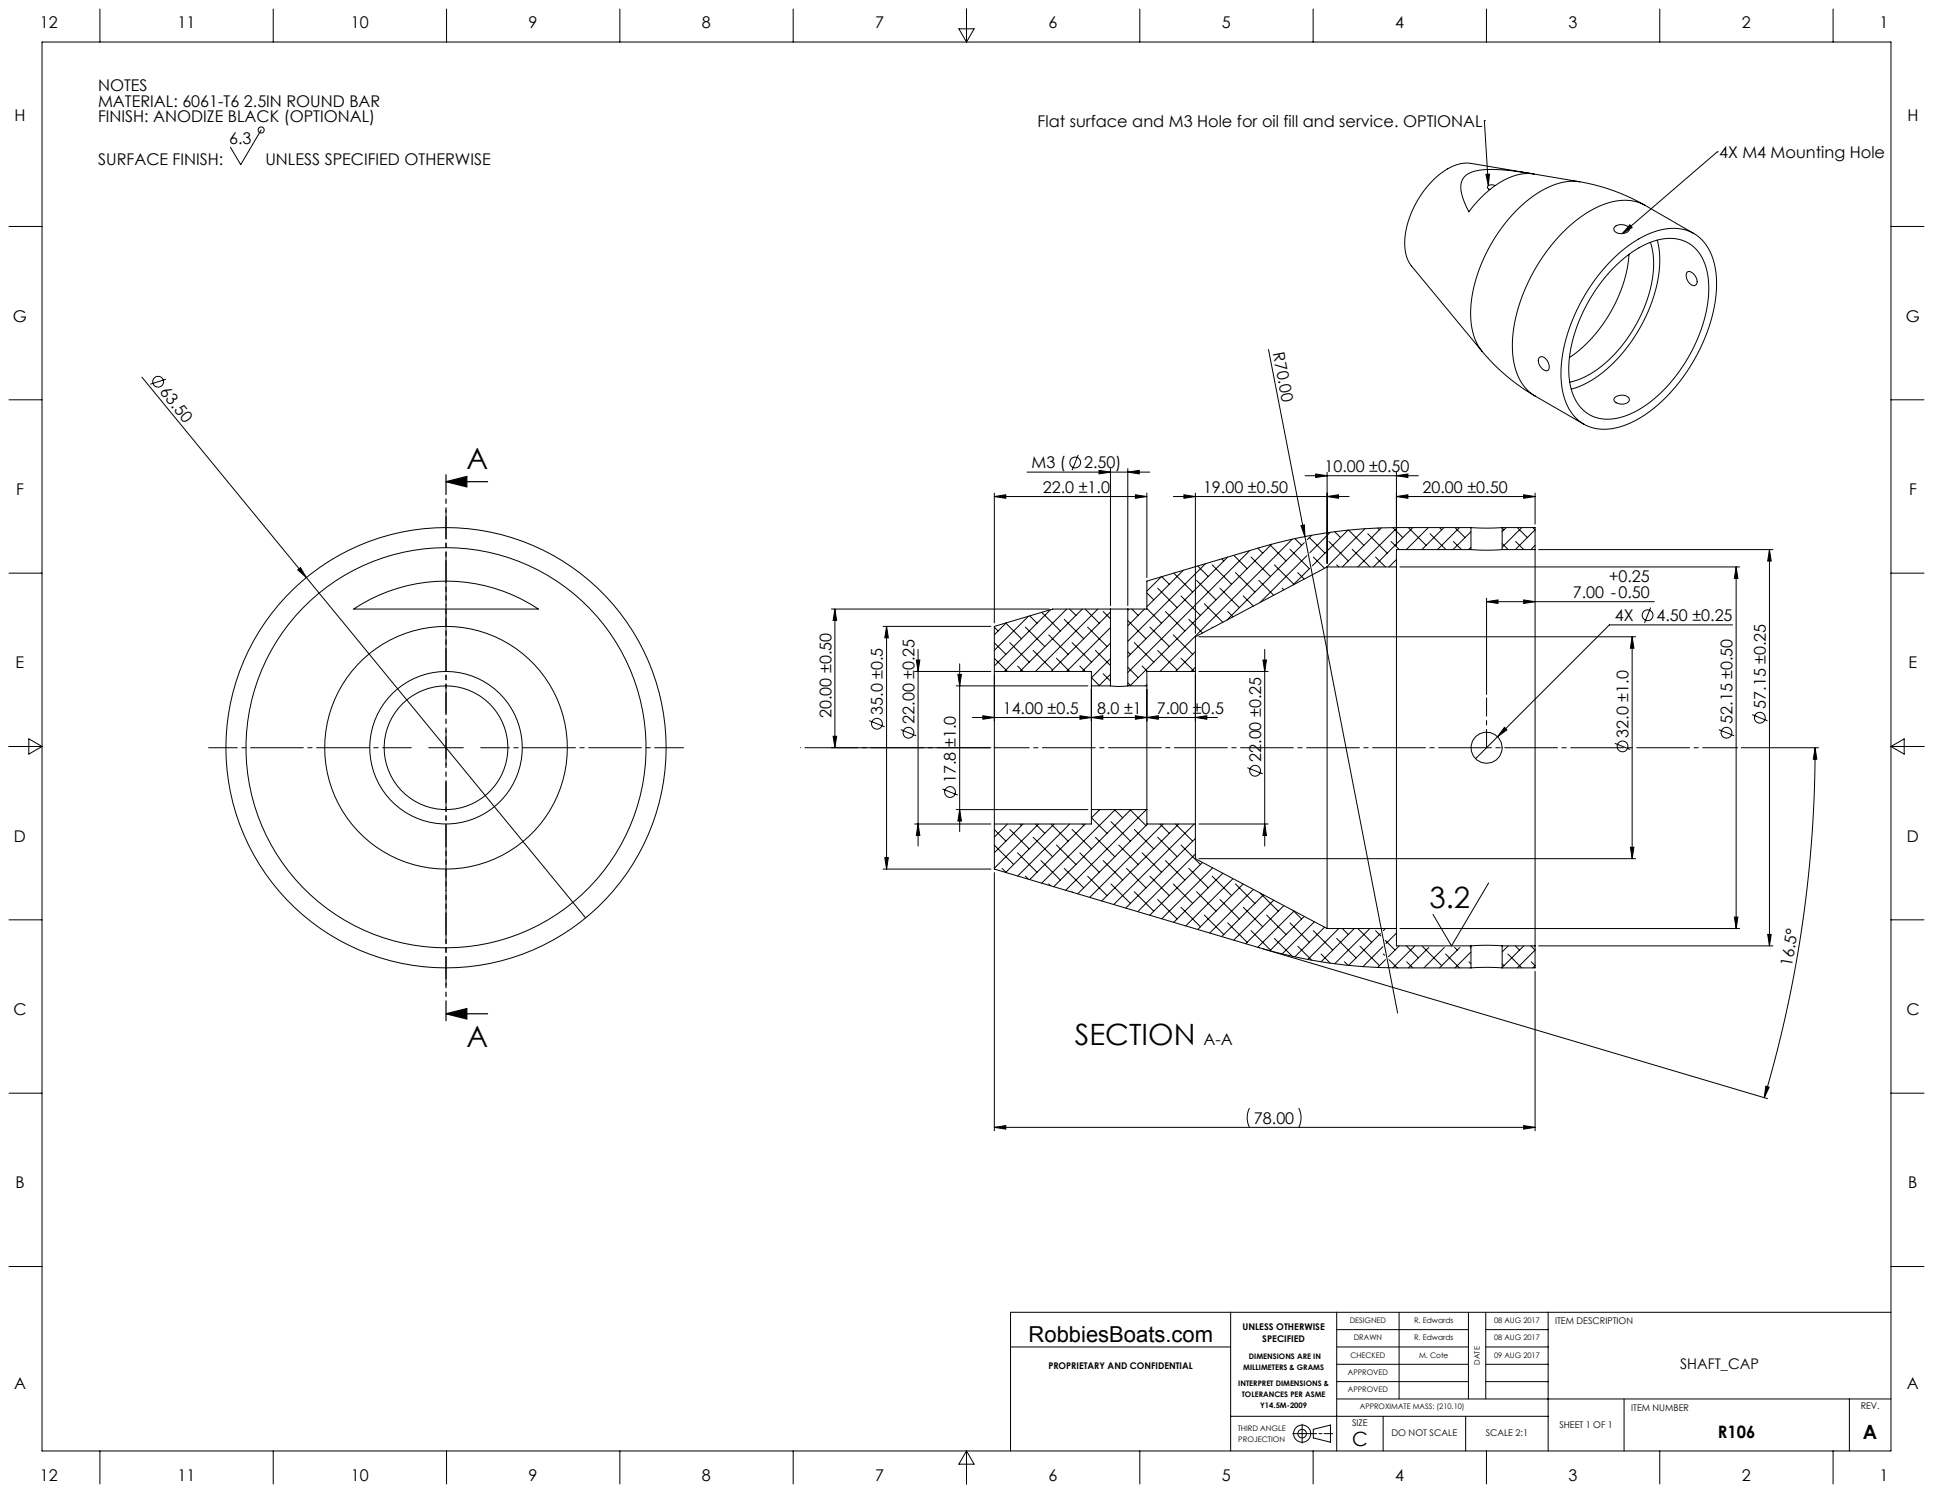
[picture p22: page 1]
4X M4 Mounting Hole; SECTION A-A; SURFACE FINISH:; THIRD ANGLE; C DO NOT SCALE; R. Edwards; M. Cote; 08 AUG 2017; 09 AUG 2017; APPROXIMATE MASS: (210.10); ITEM NUMBER; SHEET 1 OF 1; SCALE 2:1; ITEM DESCRIPTION

NOTES
MATERIAL: 6061-T6 2.5IN ROUND BAR
FINISH: ANODIZE BLACK (OPTIONAL)

Flat surface and M3 Hole for oil fill and service. OPTIONAL

UNLESS SPECIFIED OTHERWISE

UNLESS OTHERWISE
SPECIFIED
DIMENSIONS ARE IN
MILLIMETERS & GRAMS
INTERPRET DIMENSIONS &
TOLERANCES PER ASME

PROPRIETARY AND CONFIDENTIAL

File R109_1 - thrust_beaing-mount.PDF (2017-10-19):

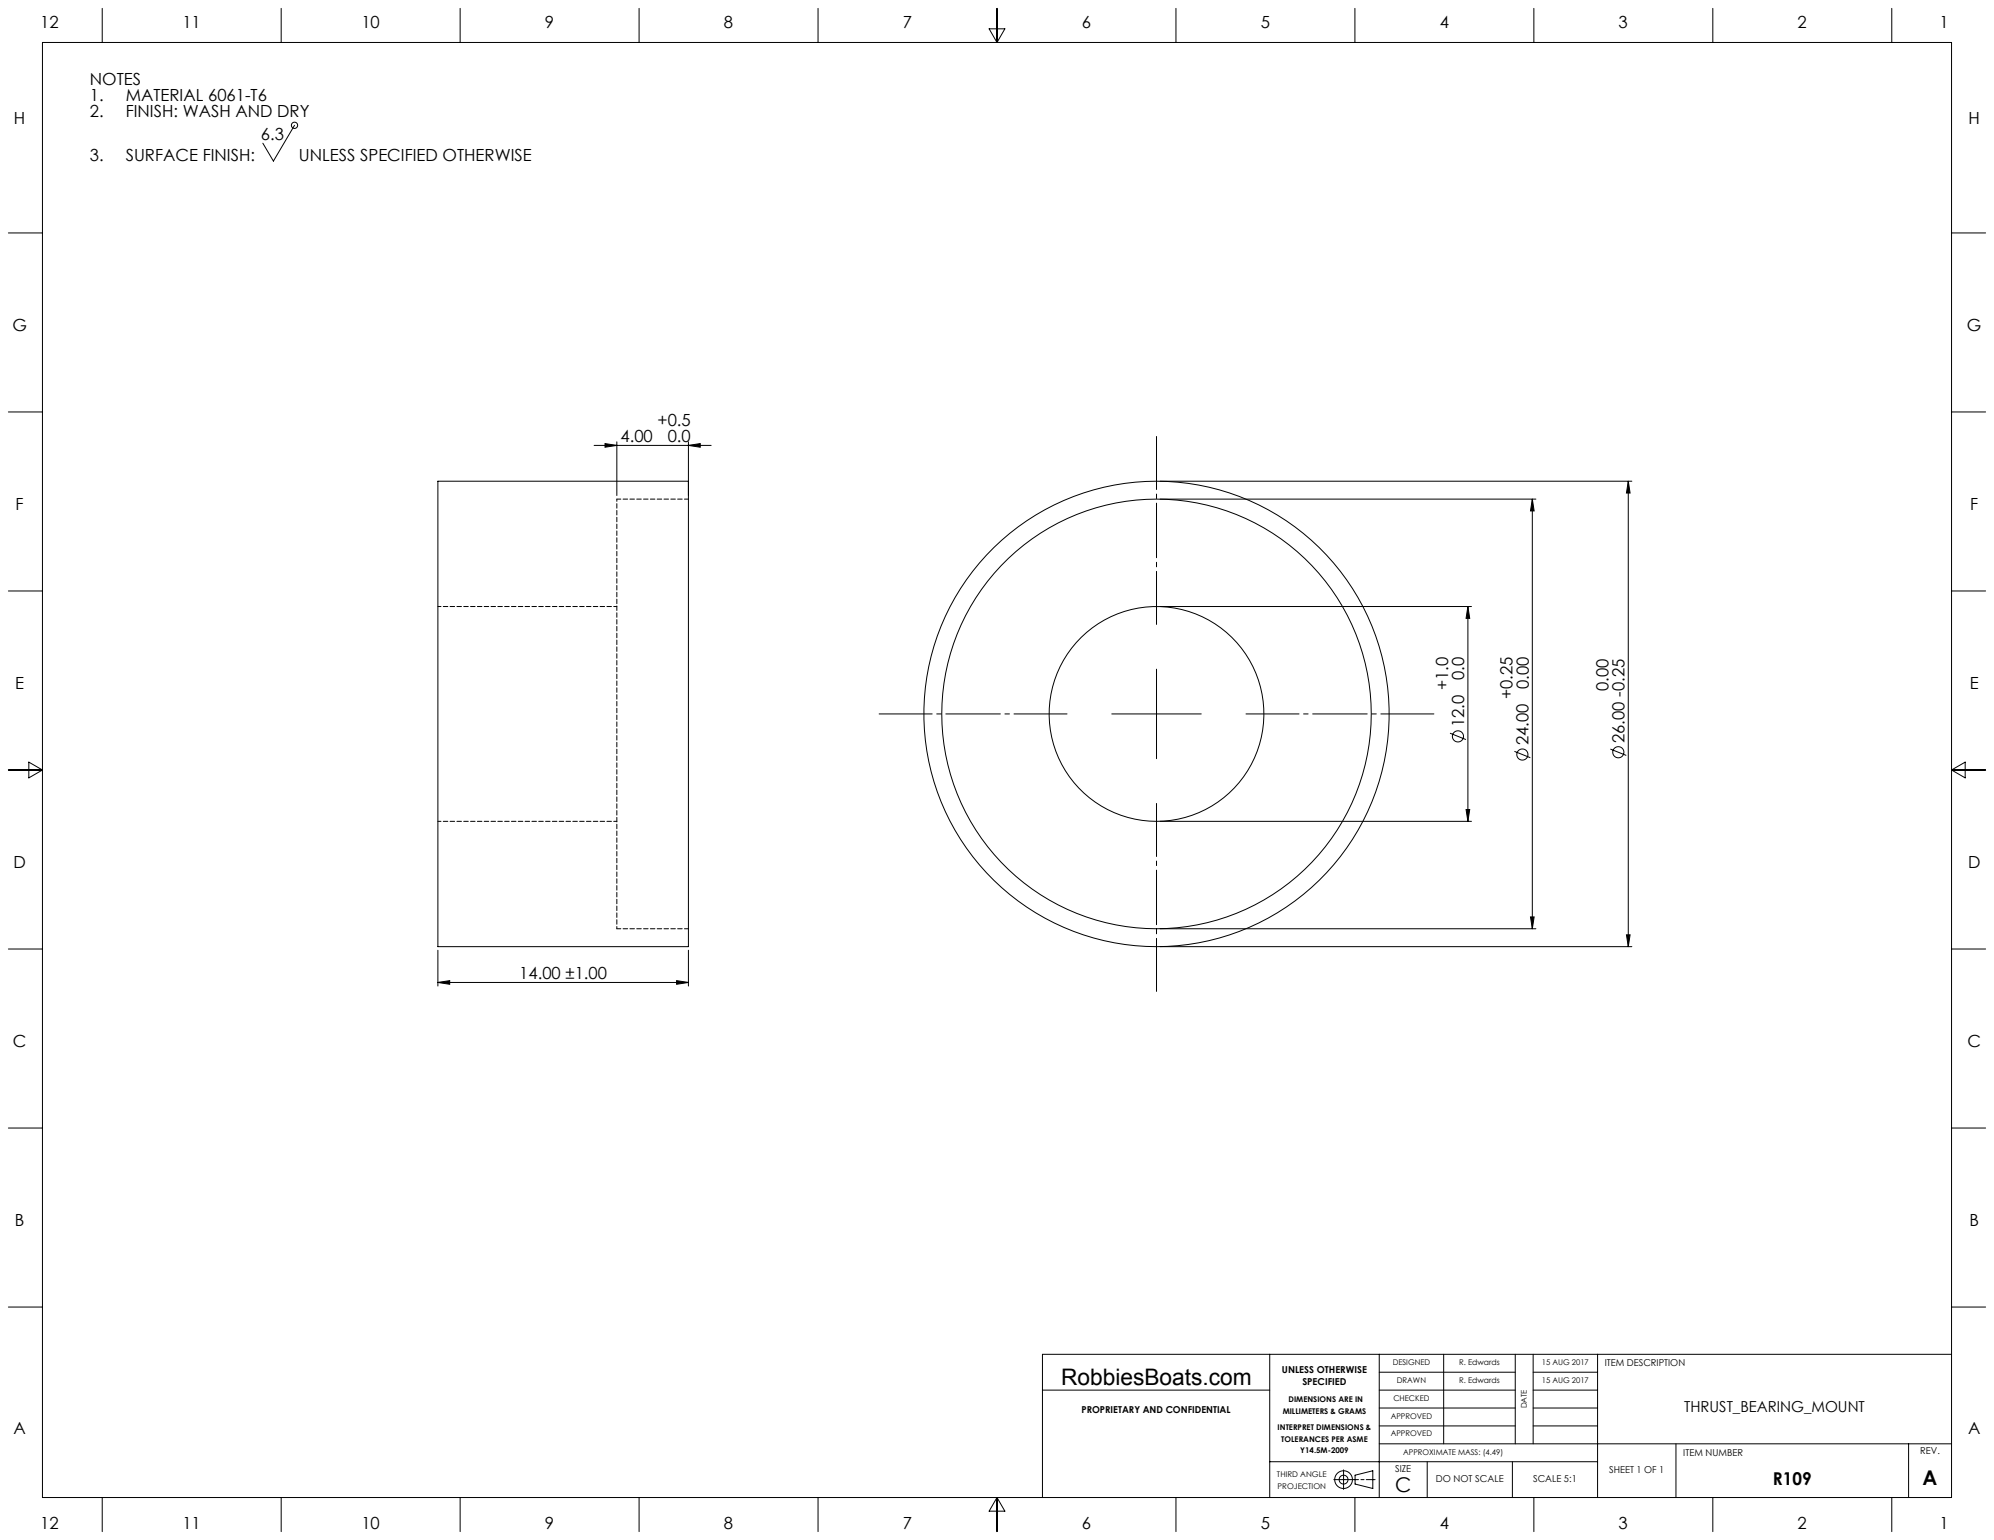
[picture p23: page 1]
SURFACE FINISH:; THIRD ANGLE; C DO NOT SCALE; R. Edwards; 15 AUG 2017; APPROXIMATE MASS: (4.49); ITEM NUMBER; SHEET 1 OF 1; SCALE 5:1; ITEM DESCRIPTION

NOTES
1. MATERIAL 6061-T6
2. FINISH: WASH AND DRY

3. UNLESS SPECIFIED OTHERWISE

UNLESS OTHERWISE
SPECIFIED
DIMENSIONS ARE IN
MILLIMETERS & GRAMS
INTERPRET DIMENSIONS &
TOLERANCES PER ASME

PROPRIETARY AND CONFIDENTIAL

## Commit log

2017-10-19 initial commit, ignore slddrw files
    [Electric Kitefoil BOM.xlsx, R101-GEO_1 - motor_tube.STEP, R102-GEO_1 - motor_gear_adapter_A.DXF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]
2017-10-19 adding propeller
    [Propeller6_2_14kn4B.STL, R110-GEO_1 - revBushing.STL]
2018-06-26 adding water intake
    [zR107-GEO_2 - nose_cone_A.STL, zR108-GEO_2 - nose_cone_B.STL]
2018-07-02 changed bolt orientation
    [R107-GEO_1 - nose_cone_A.STL, R107-GEO_2 - nose_cone_A.STL, R108-GEO_1 - nose_cone_B.STL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]
2018-07-02 add wire routing in nose cone
    [R107-GEO_2 - nose_cone_A.STL]
2018-07-10 fixed assy
    [R108-GEO_2 - nose_cone_B.STL]
2019-06-20 Adding mast wire fairing Adding mast wire fairing
    [Electric Kitefoil BOM.xlsx, Mast - wire fairing.STL, R111_1 - mast, wire fairing.STL]
